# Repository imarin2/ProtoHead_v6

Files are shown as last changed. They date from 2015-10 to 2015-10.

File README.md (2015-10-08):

# ProtoHead_v6

This repository includes the mechanical parts for a Protohead v6 DIY FABtotum head. To be fully functional it requires either the original PCB of the v4 version, or this alternative PCB:

https://github.com/imarin2/Protohead_PCB_v4_FAB_24V

# So what is this in short?

A Bowden type hotend print only FABtotum head looking like this:

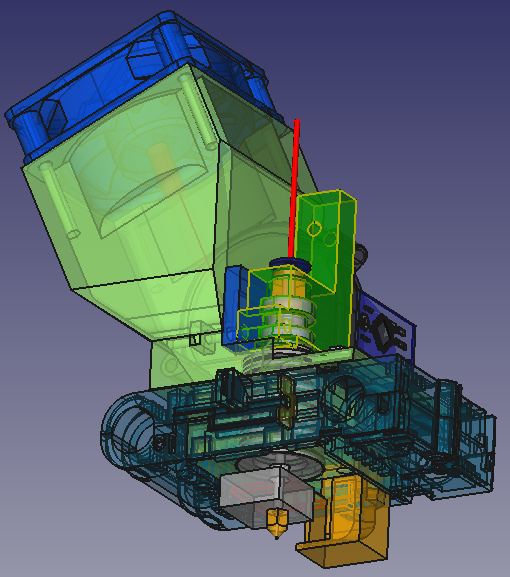
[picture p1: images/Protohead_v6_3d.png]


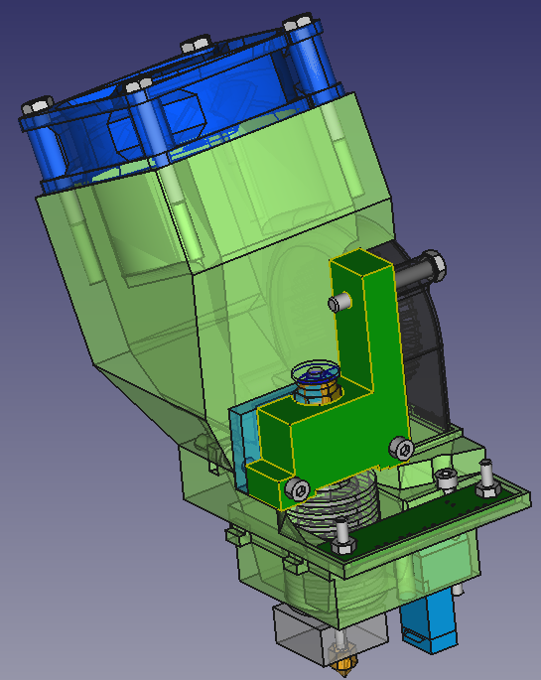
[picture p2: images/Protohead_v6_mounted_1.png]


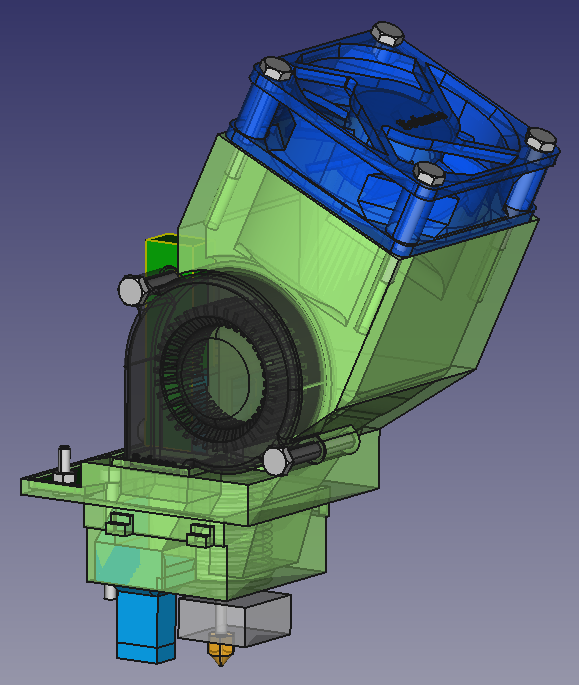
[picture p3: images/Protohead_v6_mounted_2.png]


As its v4 predecesor, it is based on a low cost almost all metal hotend with reference 3DA-002 (long version, so coming with a press-fit) and looking something like this:
https://grabcad.com/library/hotend-3da-002-1

The "mechanical design" is made in FreeCAD and the full source is included.

The design requires of an Arduino Mini Pro to be available separately and attach to the PCB via a 4 pin angled header. The I2C pins must be connected separately using a cable. The firmware for the Arduino (currently only identifying itself as 0xFFFFFFFF) is here:
https://github.com/imarin2/ProtoHead

# What does v6 improve over v4?

- A lower amount of 3d printed parts: only 4 parts. There is a bigger part (around 10 hours of print time) and the remaining parts are small and can even be printed in batch mode.
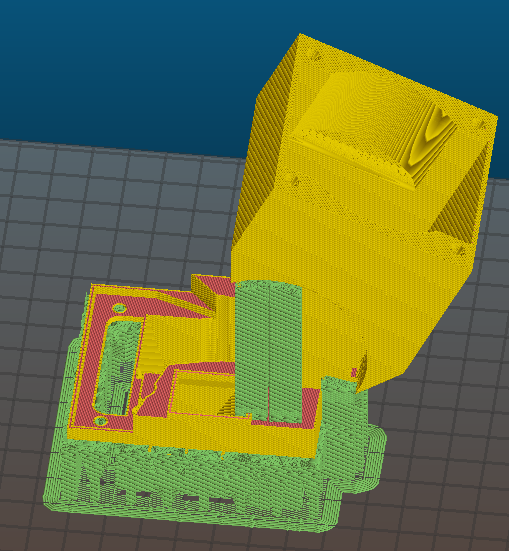
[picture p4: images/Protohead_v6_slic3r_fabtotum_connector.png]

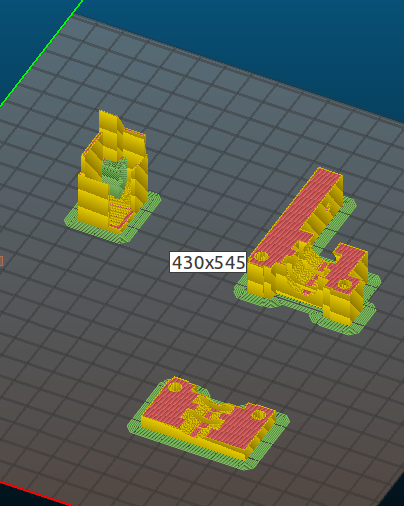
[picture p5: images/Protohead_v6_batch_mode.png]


- Reduced number of bolts and nuts, in fact only 2 M4 nuts for attachment of the extruder to the basic part and 2 M3 nuts for the PCB. The remaining M4 bolts are attached on tappered plastic.

- Improved extruder cooling: The input is very similar to v4. However the output is much more open, facilitating the out stream of hot air.

- Improved attachment of the part cooling duct using one M4 bolt.

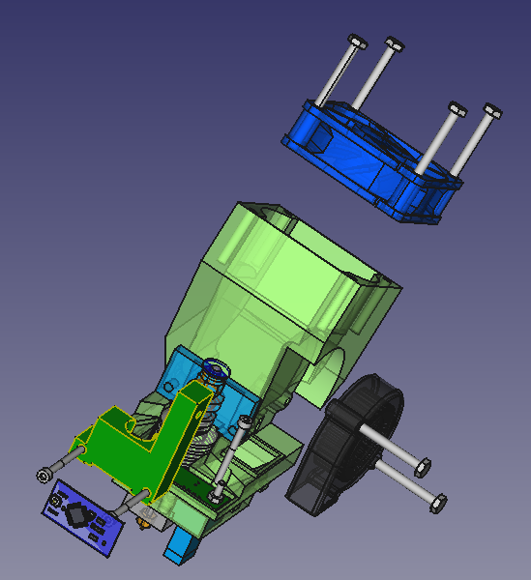
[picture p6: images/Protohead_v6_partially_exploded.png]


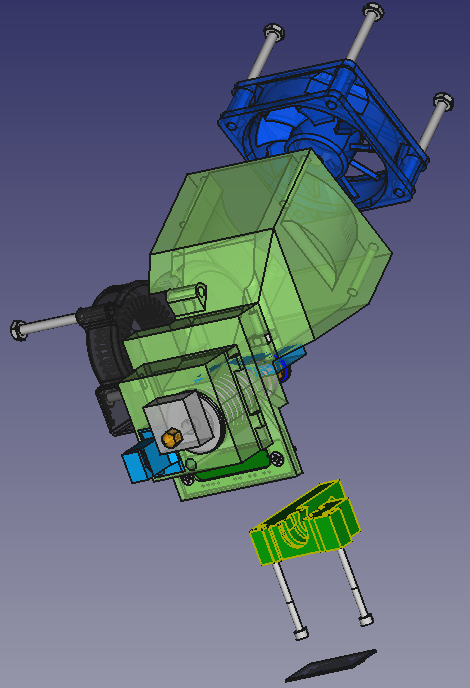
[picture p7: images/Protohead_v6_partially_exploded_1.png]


# Is this tested?
- Yes it is tested. The part cooling can be improved. A better duct design may help.

# Why are there so many STLs?

- There are two versions of the base and mount. The normal one and a 2mm offset version. The normal one is designed so that the tip is in the same position as the FABtotum hybrid head. Many persons seem to have problems that this position requires them to have the heated bed at the top-most position, which causes bad electrical contact of the heated bed. The 2mm offseted version has the nozzle point about 2 mm under the FABtotum hybrid head. Print the set that better suits you.
- There are 3 possible ducts. Take care that some ducts REQUIRE that you home on the right side of the FABtotum, as they hit on the raspicam support (it is a 2 mm thing, but still).

# What do I need to make it?
- An arduino mini pro, I have the one with the 368 chip, but any would do.
- A 3DA-002 (long version, so coming with a press-fit) with a 24V heater (sometimes is cheaper to get one with a 12V cartrige and buy a 24V cartridge separately). The thermistor that comes with them is generally a type 11 that, I hope, will be supported soon in FABlin if my last pull-request is merged.
- A 5V blower fan 5015S DC 5V 50x50x15mm
- An axial fan 60x60 mm, 5V.
- M4 and M3 bolts and nuts of different sizes (I will hopefully make a list some day, see the FreeCAD source). Better than the hex screws is to use hex socket (allen, imbus) screws.

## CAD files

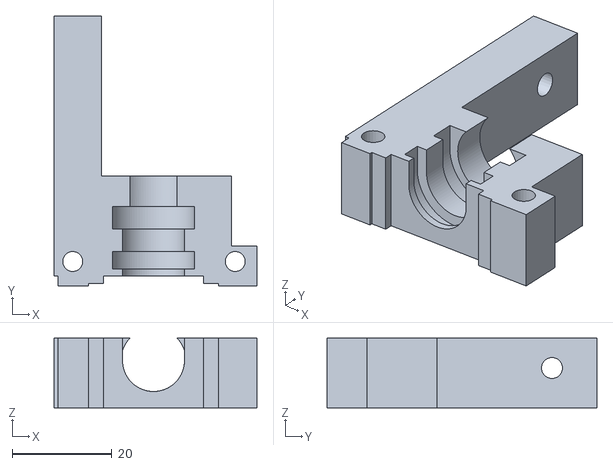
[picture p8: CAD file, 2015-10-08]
Improved_Extruder_base_2mm_offset.stl
40.6 x 54.0 x 14.0

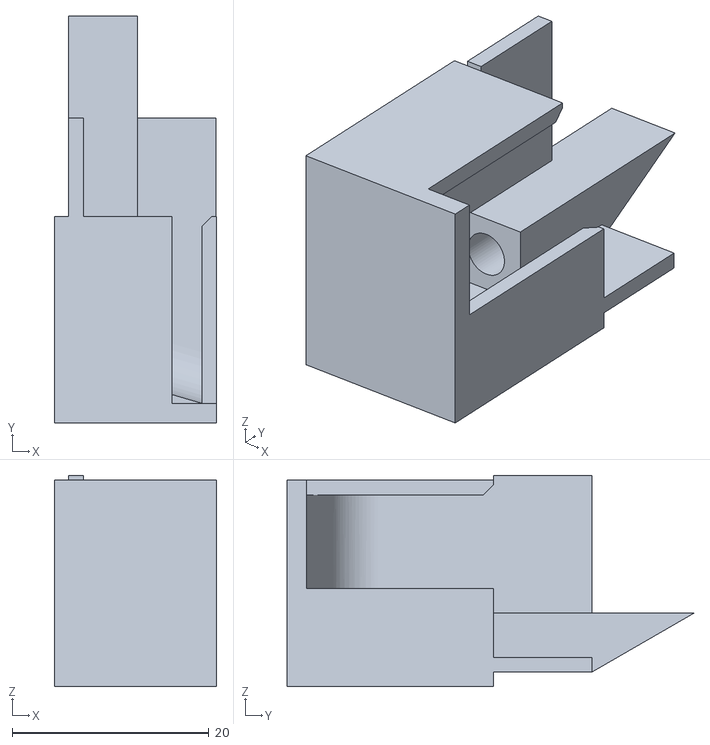
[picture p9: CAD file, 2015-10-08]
Improved_external_blower_duct.stl
16.5 x 41.4 x 21.5

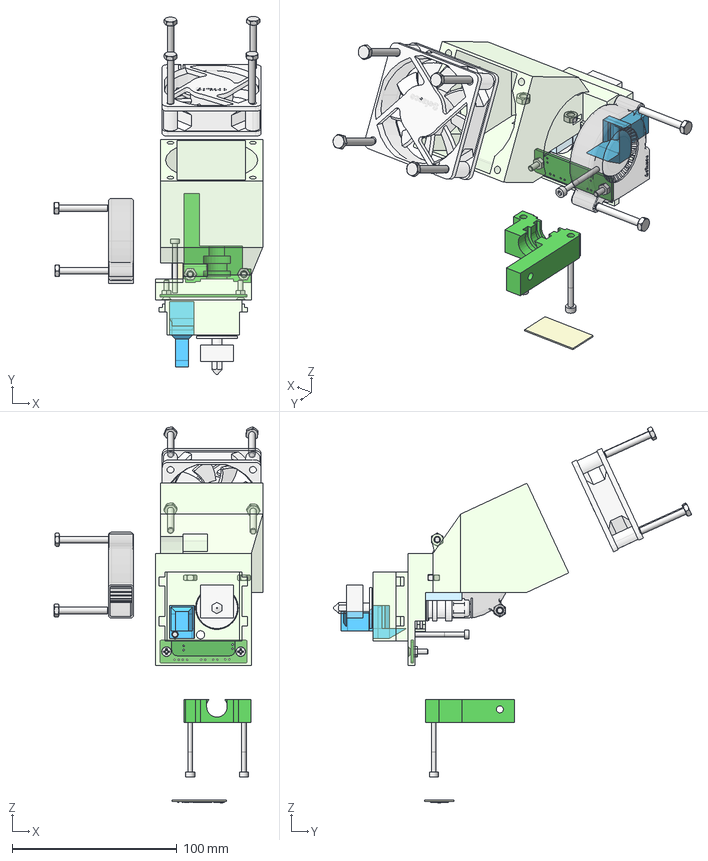
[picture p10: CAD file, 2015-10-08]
Protohead_v6_Bowden_offset-2mm_exploded.fcstd
126.5 x 217.3 x 228.1 mm
Improved_Fabtotum_connector
Improved_external_blower_duct_3
Improved_extruder_mount
Improved_Extruder_base
Axial_fan_with_ray
Chinese_long_distance_extruder_Hotend 3DA-002
Arduino_Mini
DB5015_BLOWER_FAN
M4x30_fan_1
M4x30_fan_002
M4x30_fan_003
M4x30_fan_004
M4x30_003
M4x30_004
Hex socket head cap screw M4 30_1
Hex socket head cap screw M4 30_002
M4_nut_001
M4_nut_002
PCB_attachment_M3_nut_1
PCB_attachment_M3_nut_2
PCB_attachment_M3_3x12_1
Board_outline001
PCB_attachment_M3_3x12_2
Hex socket head cap screw M4 30_003

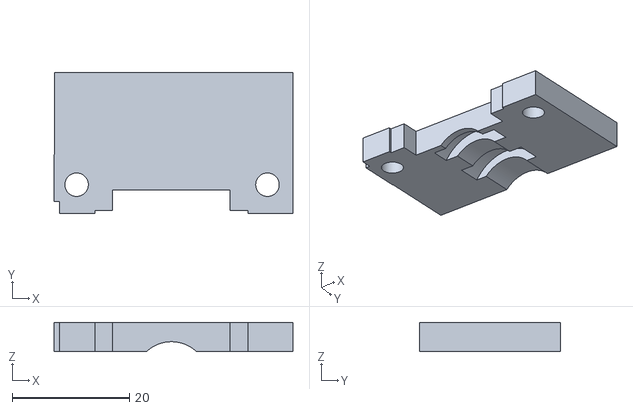
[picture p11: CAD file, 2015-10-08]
Improved_extruder_mount.stl
40.7 x 24.0 x 5.00

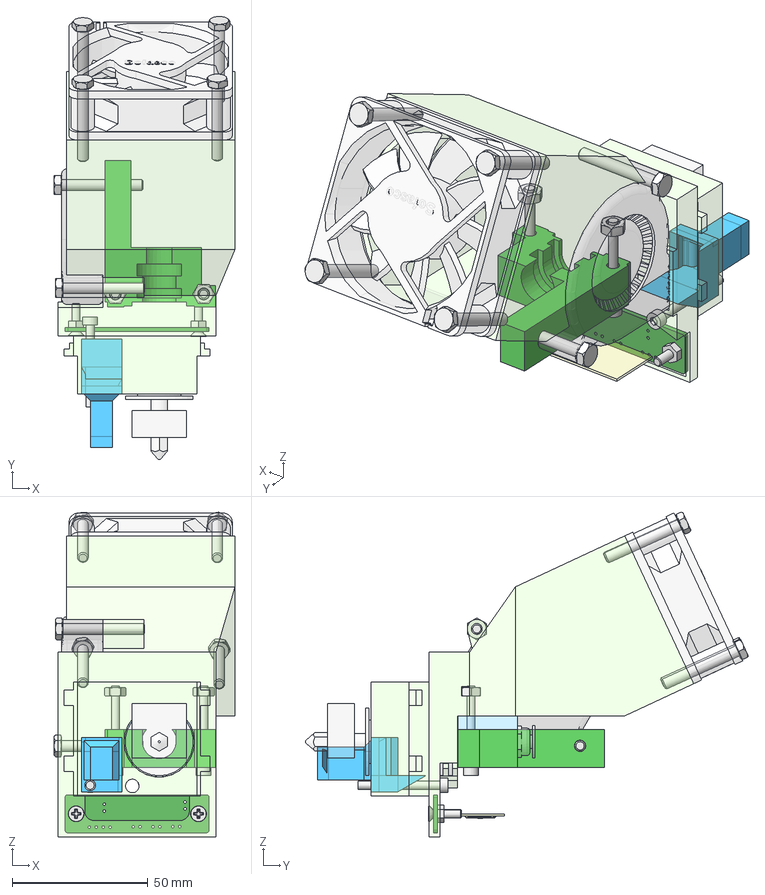
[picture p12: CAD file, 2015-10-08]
Protohead_v6_Bowden_offset-2mm_parts_only.fcstd
66.5 x 162.9 x 119.5 mm
Improved_Fabtotum_connector
Improved_external_blower_duct_3
Improved_extruder_mount
Improved_Extruder_base
Axial_fan_with_ray
Chinese_long_distance_extruder_Hotend 3DA-002
Arduino_Mini
DB5015_BLOWER_FAN
M4x30_fan_1
M4x30_fan_002
M4x30_fan_003
M4x30_fan_004
M4x30_003
M4x30_004
Hex socket head cap screw M4 30_1
Hex socket head cap screw M4 30_002
M4_nut_001
M4_nut_002
PCB_attachment_M3_nut_1
PCB_attachment_M3_nut_2
PCB_attachment_M3_3x12_1
Board_outline001
PCB_attachment_M3_3x12_2
Hex socket head cap screw M4 30_003

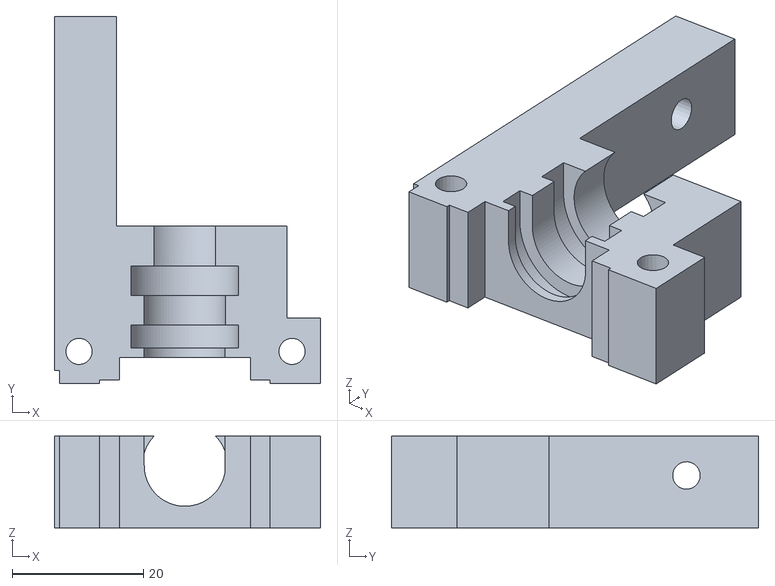
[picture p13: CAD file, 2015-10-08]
Improved_Extruder_base.stl
40.6 x 56.0 x 14.0

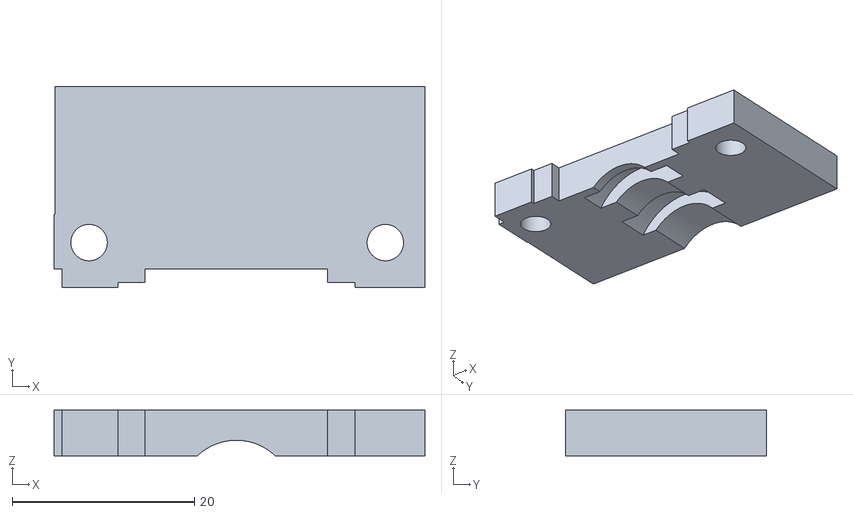
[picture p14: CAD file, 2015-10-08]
Improved_extruder_mount_2mm_offset.stl
40.7 x 22.0 x 5.00

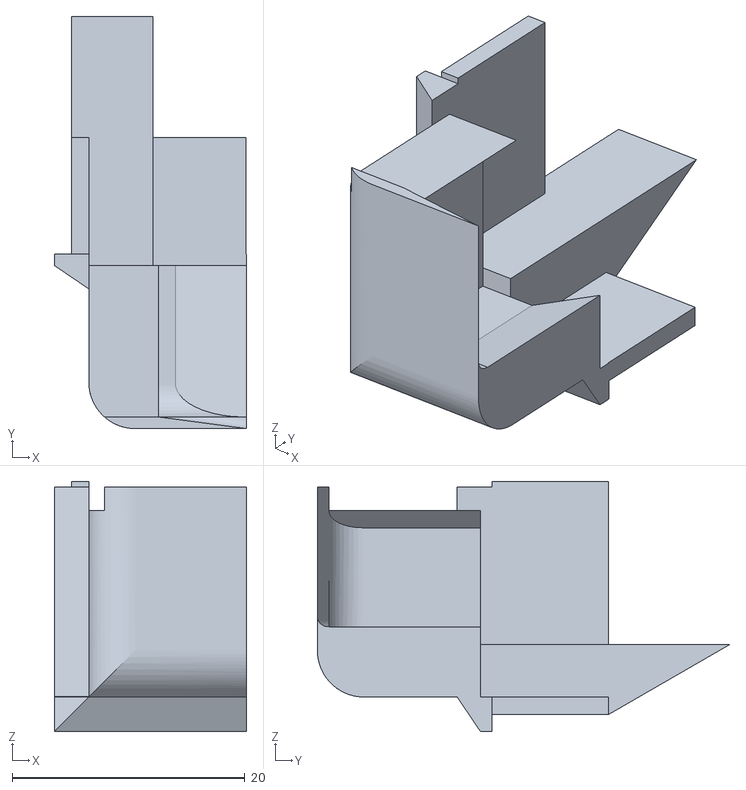
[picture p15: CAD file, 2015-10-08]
Improved_external_blower_duct_2.stl
16.5 x 35.4 x 21.5

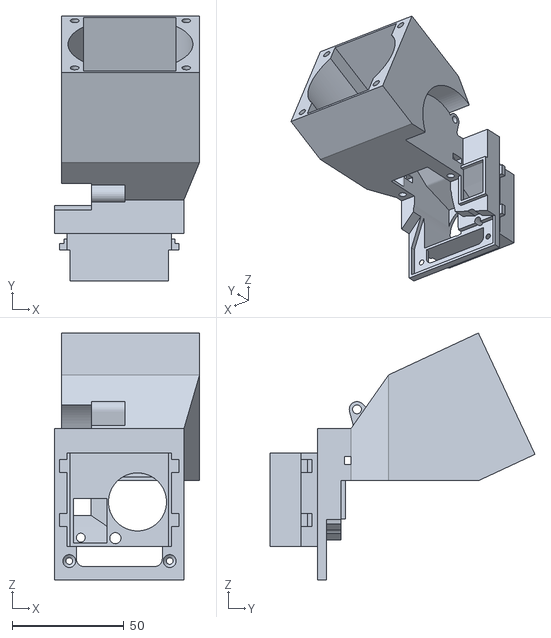
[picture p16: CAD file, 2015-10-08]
Improved_Fabtotum_connector.stl
65.1 x 118.8 x 110.7

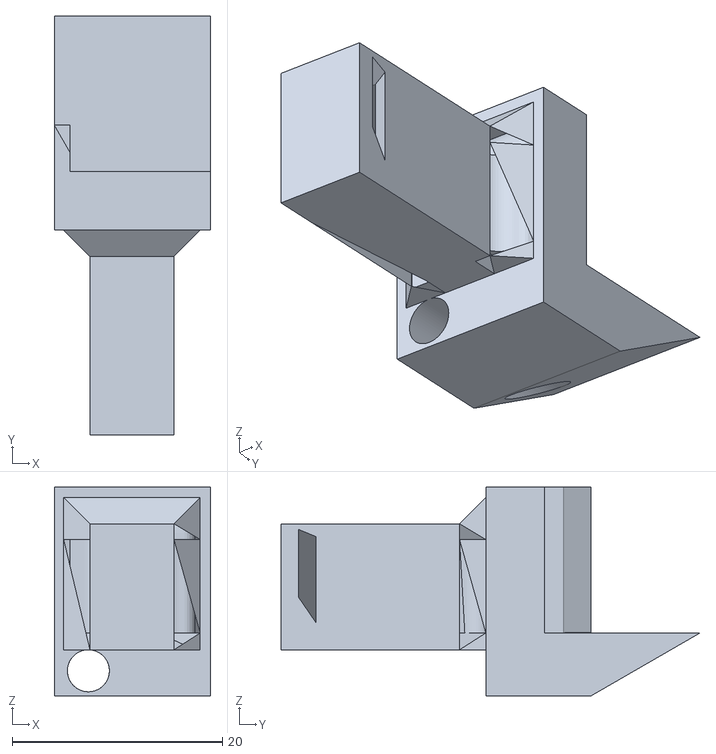
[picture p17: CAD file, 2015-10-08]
Improved_external_blower_duct_3.stl
14.9 x 39.9 x 19.9
